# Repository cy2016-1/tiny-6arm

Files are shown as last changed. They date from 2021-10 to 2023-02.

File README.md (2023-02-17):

### 一、机械臂简介

机械制作方面采用铝型材、3D打印、同步带和步进电机，低成本的制作方案。控制器方面，使用esp32s3芯片，带有WiFi蓝牙功能。可以输出100KHZ脉冲，支持关节运动和直线运动指令，150mA 8路输出，6~36V 8路输入，带光耦隔离。编程方面，采用blockly可视化编程，使用手机或平板就可以完成编程。

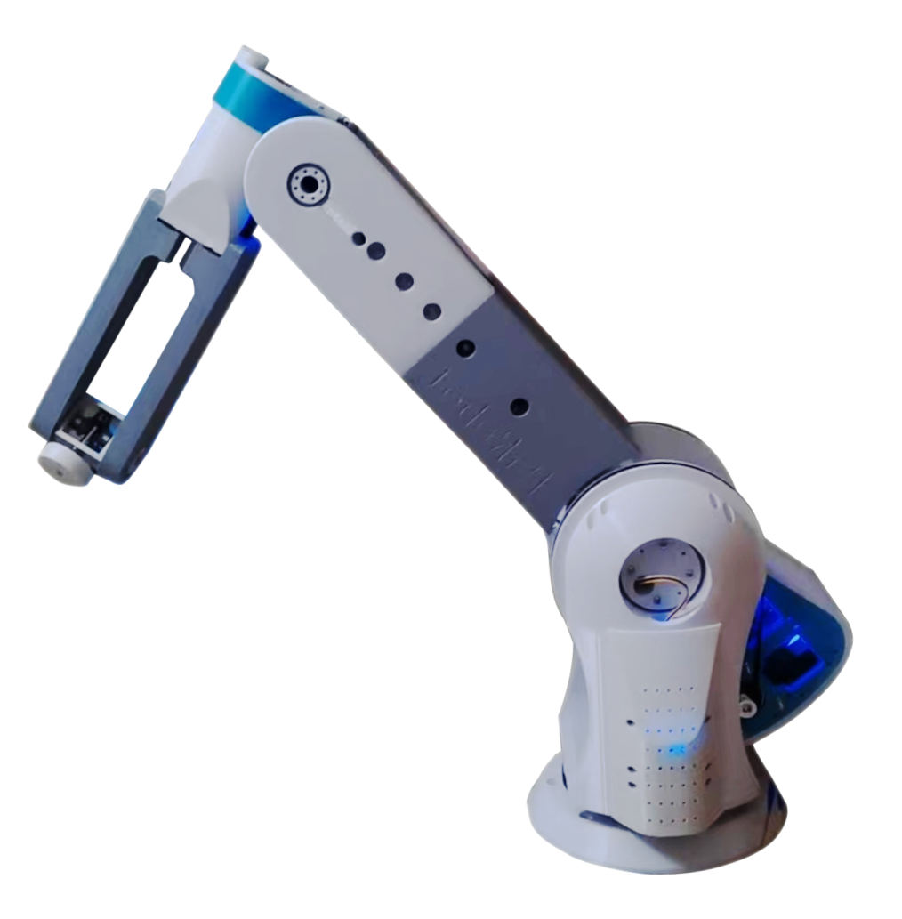
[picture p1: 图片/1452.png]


### 二、制作过程

#### 1.机械部分

首先使用FreeCAD软件进行3D模型图绘制。FreeCAD是一个开源的3D设计软件，可以免费使用，方便二次开发，支持运动仿真和简单的有限元仿真。我使用它来设计我的机械臂。其中前三关节采用双电机结构，也就是说一个关节有两个电机，这样平衡的设计既提高了负载能力，也提高了精度和稳定性。现在这台机械臂拥有3kg负载能力和0.5mm的重複定位精度，以及765mm的臂长。

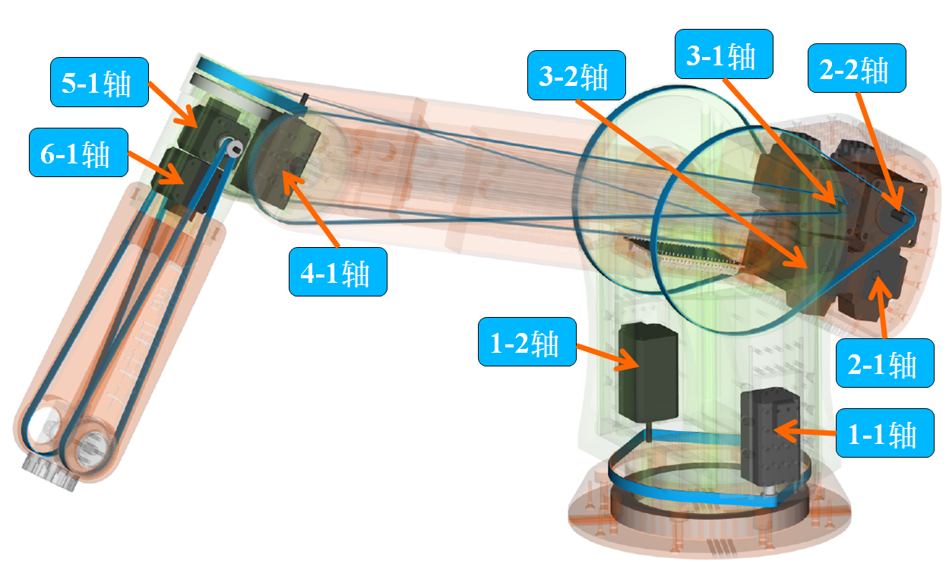
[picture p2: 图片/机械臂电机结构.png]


#### 2.控制器部分

##### 2.1 主控制器

主控制器采用ESP32-S3芯片，ESP32-S3芯片带有WiFi蓝牙功能，双核，240Mhz频率，45 个可编程 GPIO。性能可以满足机械臂运行算法，设计了6个脉冲控制接口，可以控制6轴机械臂。8路输入和8路输出，带光电耦合起到保护电路的作用，方便外接电磁阀。

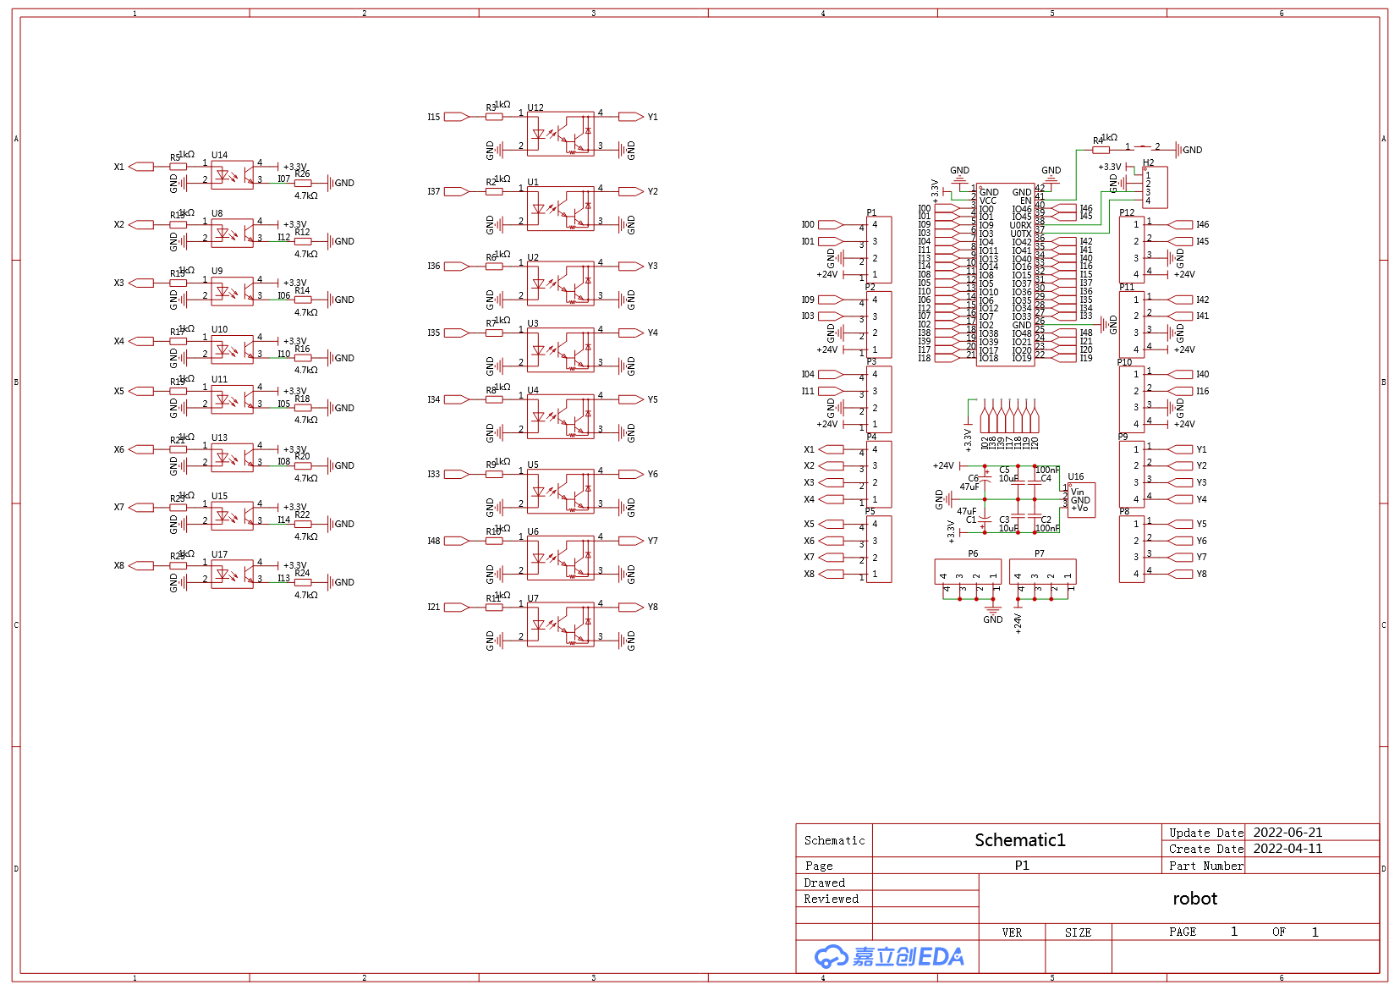
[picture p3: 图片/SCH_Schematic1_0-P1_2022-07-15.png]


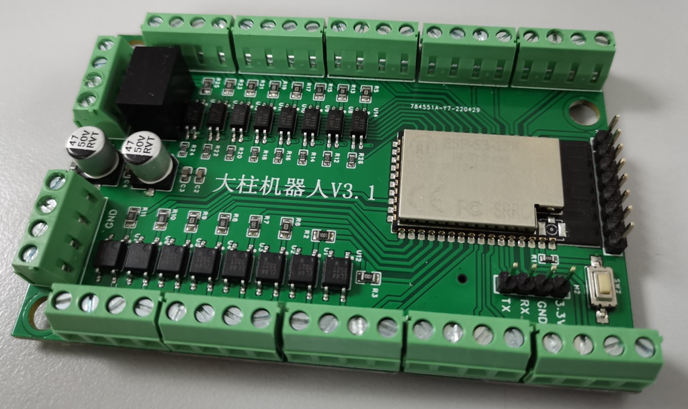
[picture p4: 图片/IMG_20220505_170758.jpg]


##### 2.2 电机驱动部分

步进电机驱动采用TB67S109AFTG芯片，支持最大4A电流。控制芯片使用ESP32-C3，支持脉冲控制和CAN通信控制。磁编码器使用MT6816CT-ACD，14位单圈绝度编码器，最高精度可达0.02°。

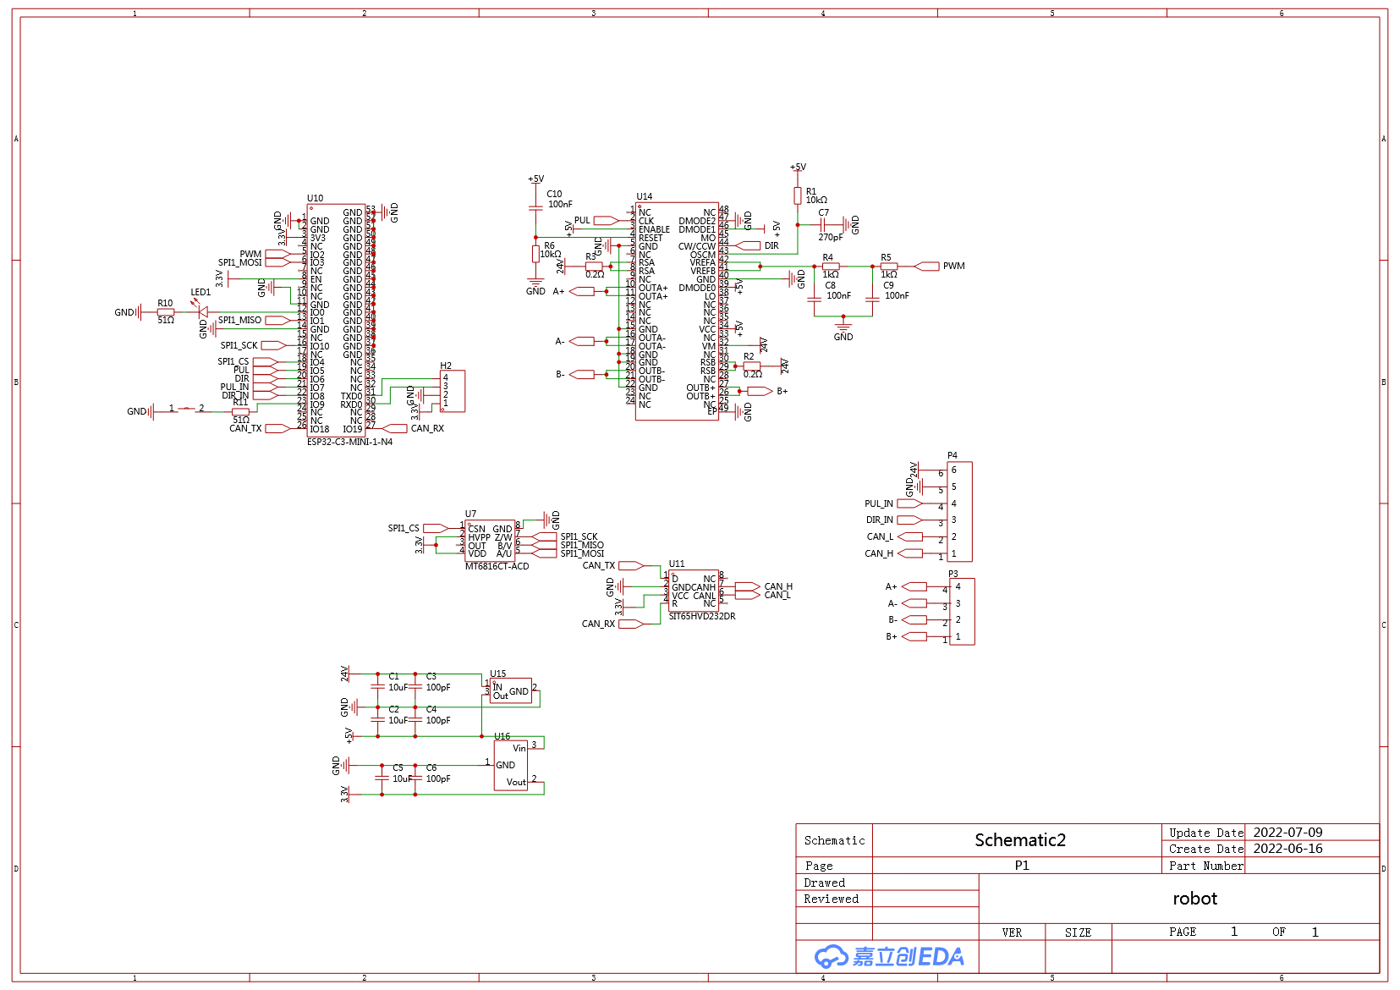
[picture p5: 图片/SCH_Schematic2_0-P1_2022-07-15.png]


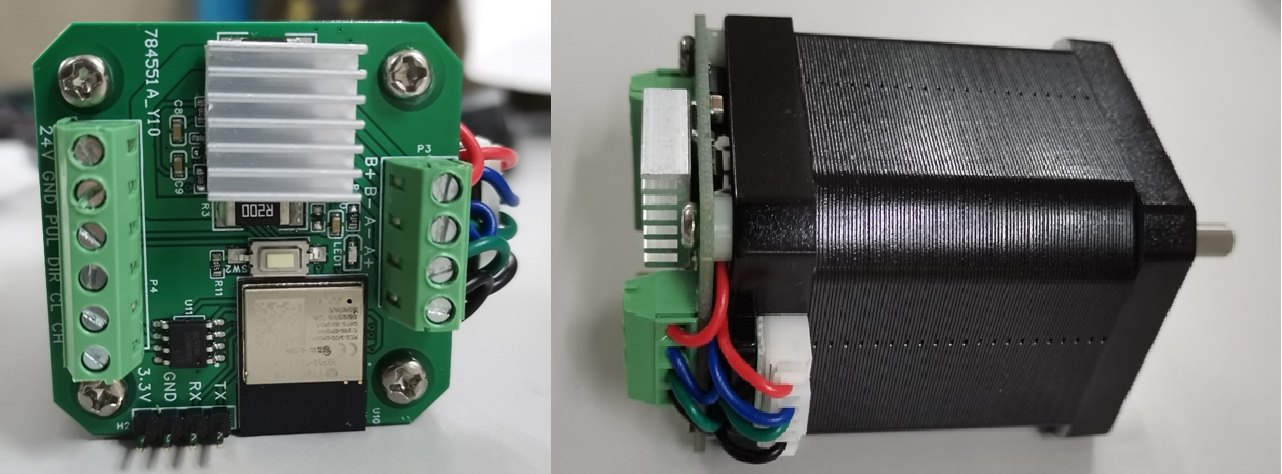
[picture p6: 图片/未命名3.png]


##### 2.3 软件部分

主控板程序是基于开源micropython的，它实现了使用python语言就可完成单片机程序开发。驱动板编程是基于ESP-IDF库编写的C语言程序。手机控制软件是基于开源blockly和bipes编写的。

软件下载时使用USB转串口下载，电机驱动板下载前按住按键然后上电进入下载模式，下载完成后需要校准编码器。校准方法是：电机无负载上电 >> 蓝色LED亮时按住按键 >> 进入自动校准模式。

| 电路板 | 程序 | 固件 |
|---|---|---|
| 控制器 | robot.c | robot.bin |
| 1-1轴 | step1-1.c  | step1-1.bin |
| 1-2轴 | step1-2.c  | step1-2.bin |
| 2-1轴 | step2-1.c  | step2-1.bin |
| 2-2轴 | step2-1.c  | step2-2.bin |
| 3-1轴 | step3-1.c  | step3-1.bin |
| 3-2轴 | step3-2.c  | step3-2.bin |
| 4-1轴 | step4-1.c  | step4-1.bin |
| 5-1轴 | step5-1.c  | step5-1.bin |
| 6-1轴 | step6-1.c  | step6-1.bin |

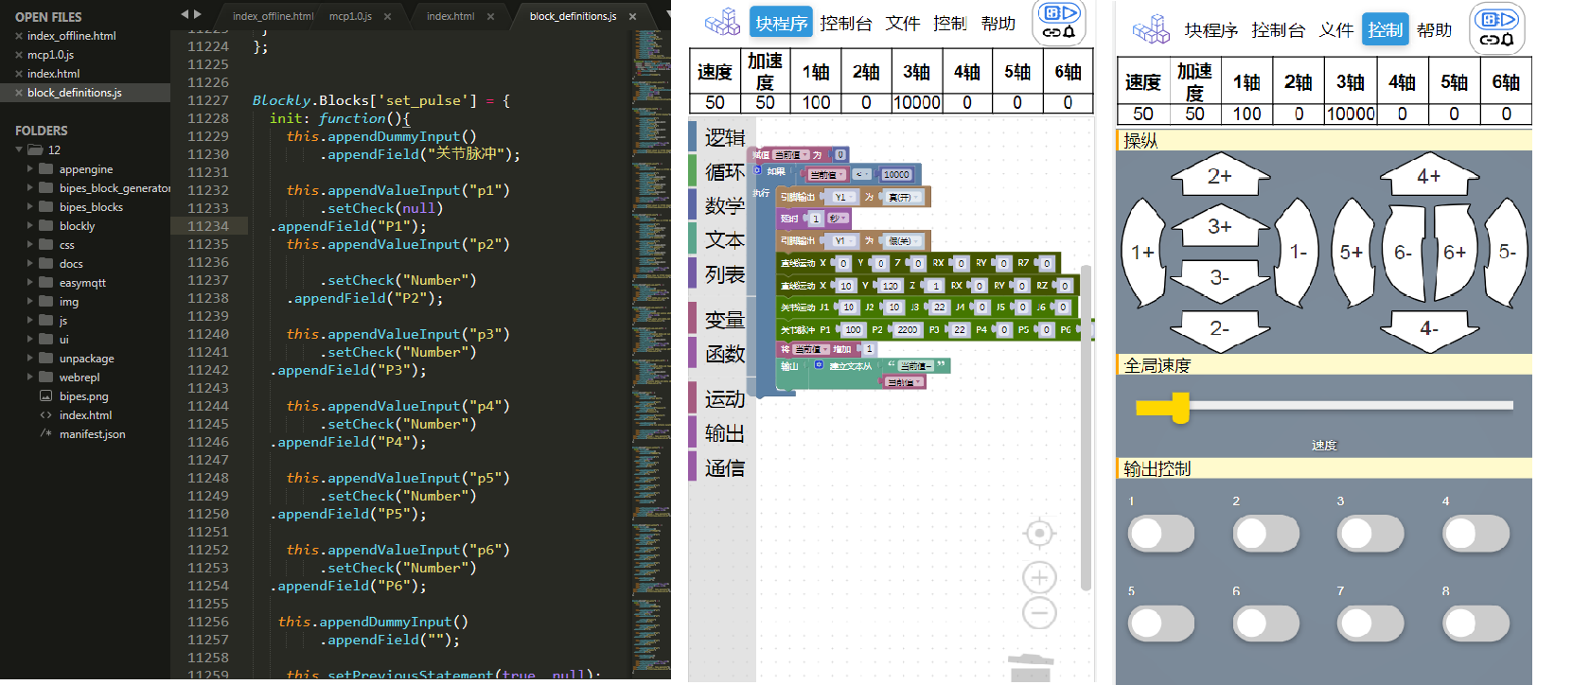
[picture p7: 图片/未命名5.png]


### 三、使用说明

注意：用手拖动到初始位置再通电，此时作为坐标原点。

#### 3.1 手机或平板编程

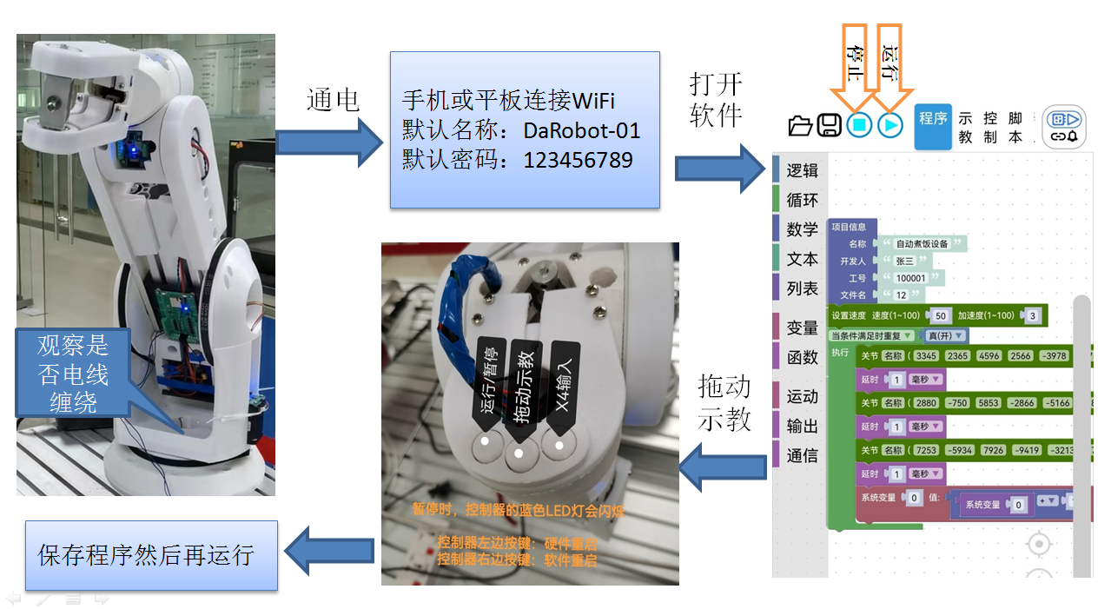
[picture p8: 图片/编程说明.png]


#### 3.2 电脑编程（Thonny软件）

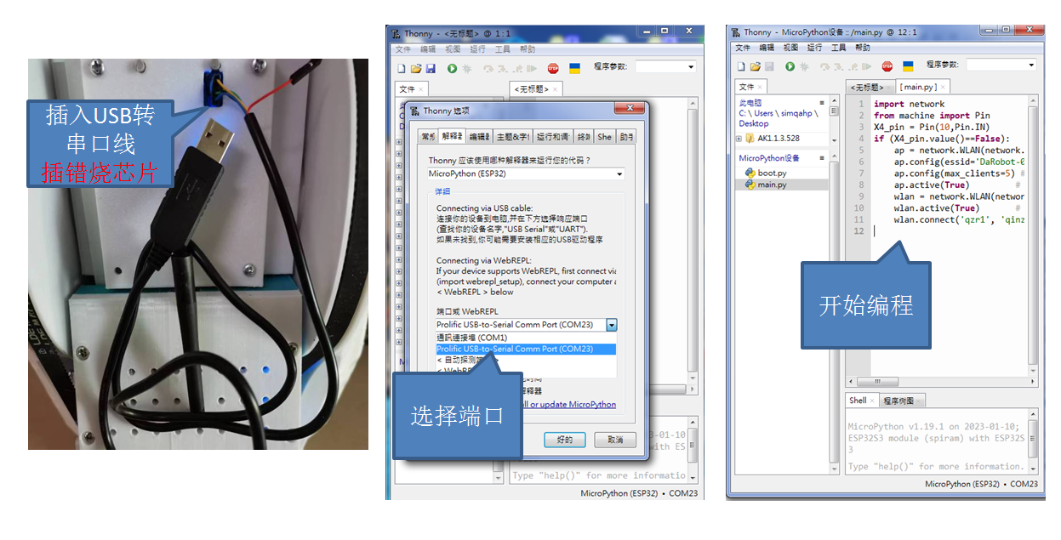
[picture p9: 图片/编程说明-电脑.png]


#### 3.3 RS485通信

控制板带有RS485通信接口，可以使用modbus协议控制和读取机械臂的状态

默认参数：波特率：9600，数据位：8，校验：无，停止位：1，modbus站口：1

| 地址 | 读/写 | 说明 |
|---|---|---|
| 0~99 | 读/写 | 系统变量，支持断电保存 |
| 100~149 | 读/写 | 未使用  |
| 150 | 读/写 | 机械臂全局速度 |
| 151 | 读 | 机械臂实时速度 |
| 152 | 读/写 | 机械臂目标速度 |
| 153 | 读 | 机械臂实时加速度 |
| 152 | 读/写 | 机械臂目标加速度 |
| 160~165 | 读 | 机械臂6个关节实时脉冲数  |
| 170~175 | 读/写 | 机械臂6个关节目标脉冲数  |
| 180~185 | 读 | 机械臂6个关节实时力矩  |
| 190 | 读/写 | 设置modbus波特率： 0:9600, 1:19200, 2:38400, 3:57600, 4:112500 |
| 191 | 读/写 | 设置modbus数据位： 0:8位,  1:7位 |
| 192 | 读/写 | 设置modbus校验： 0:无校验, 1:奇校验, 2:偶校验|
| 193 | 读/写 | 设置modbus停止位： 0:1位,  1:2位 |
| 194 | 读/写 | 设置modbus站口，默认是1，  范围：1~256 |

### 四、项目收入

| 时间 | 收入类型 | 金额（元） |
|---|---|---|
| 2021-2022 | 嘉立创-星火计划金奖 | 10000|
| 2021-2022 | 用户咨询赞助 | 500 |
| 2021-2022 | 哔哩哔哩视频 |  100 |
| 2020-2021 | 贸泽电子-短视频大赛金奖 | 2000  |
| 2020-2021 | 用户咨询赞助 | 200 |
| 2020-2021 | 哔哩哔哩视频 | 200 |

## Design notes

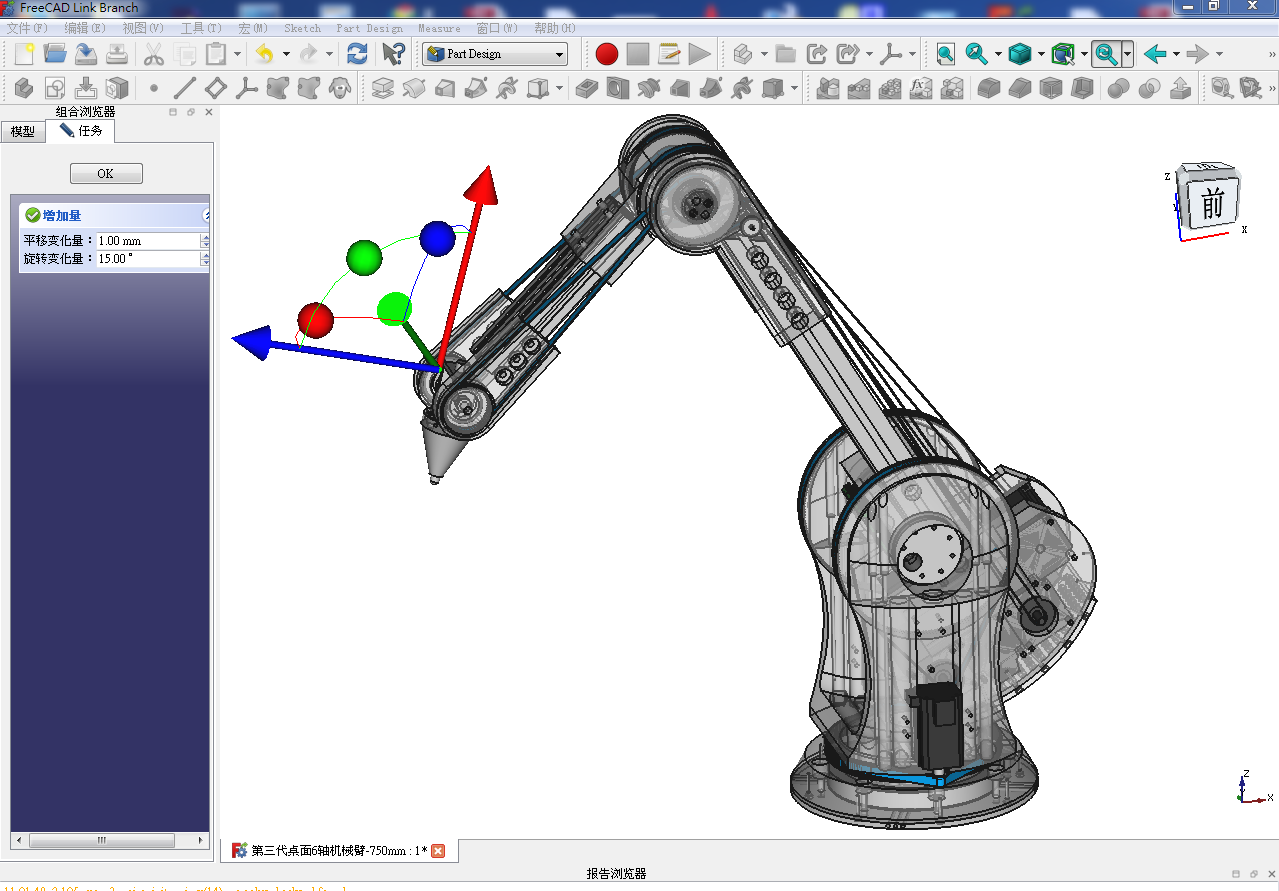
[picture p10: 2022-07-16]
图片未命名.png

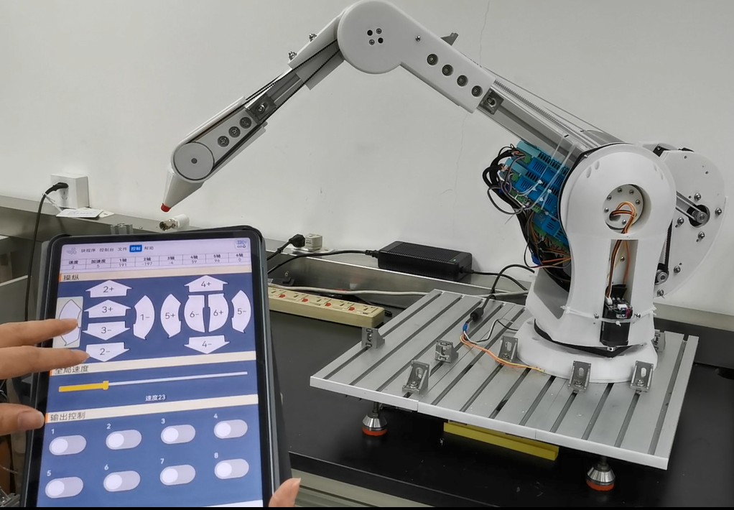
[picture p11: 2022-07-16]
图片/未命名4.png

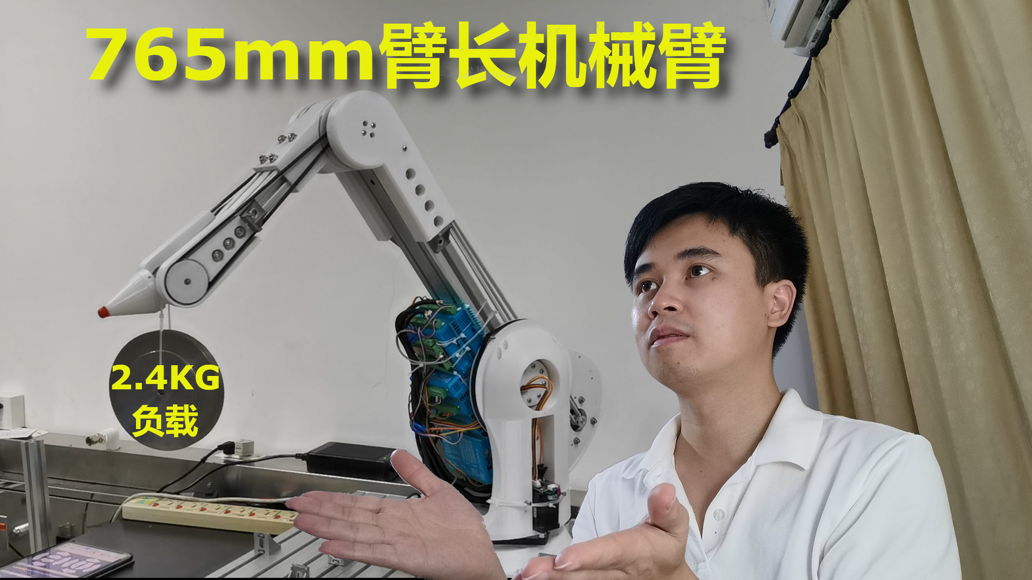
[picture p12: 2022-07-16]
图片/无标题8.png

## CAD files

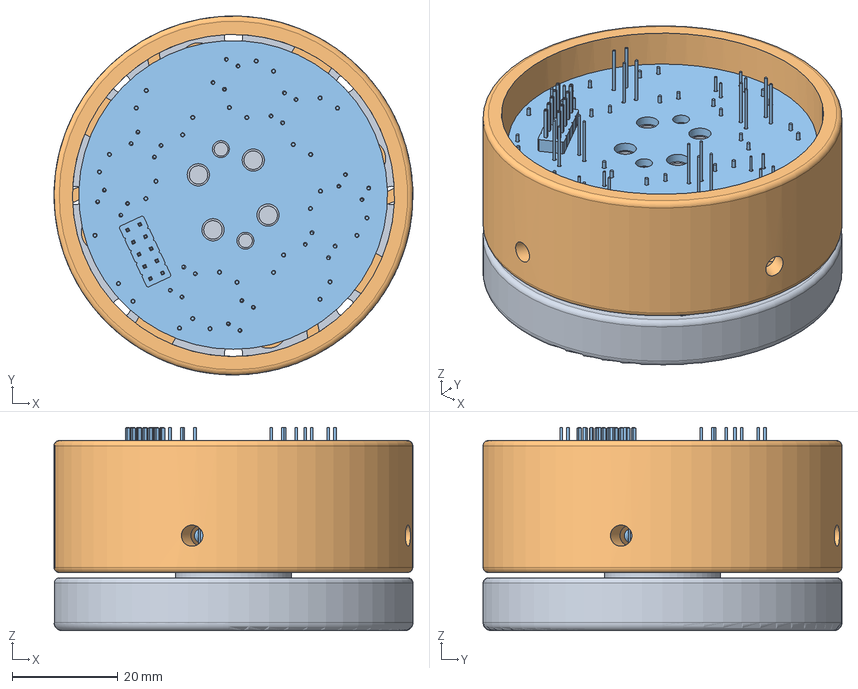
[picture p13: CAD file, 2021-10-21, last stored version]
3D模型图/力传感器.FCStd
68.0 x 68.0 x 38.5 mm
力传感器

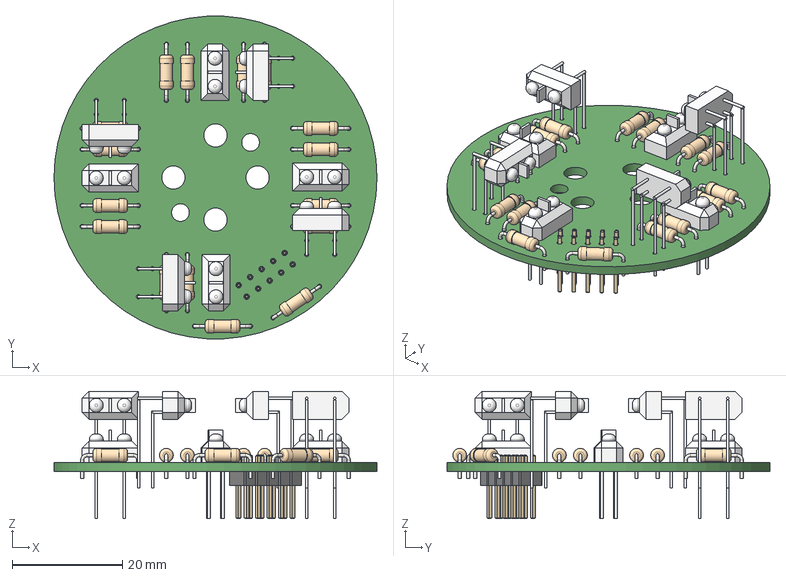
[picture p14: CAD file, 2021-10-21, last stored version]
力传感器电路图/力传感器.step
58.5 x 58.4 x 23.1 mm

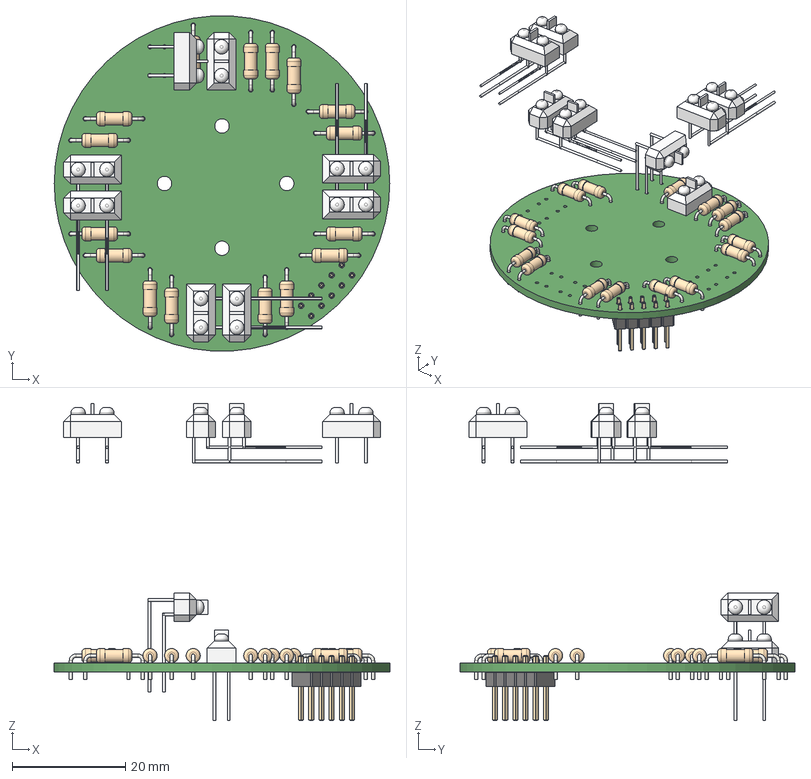
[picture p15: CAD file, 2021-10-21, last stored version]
力传感器电路图/力传感器22.step
59.2 x 59.1 x 56.0 mm

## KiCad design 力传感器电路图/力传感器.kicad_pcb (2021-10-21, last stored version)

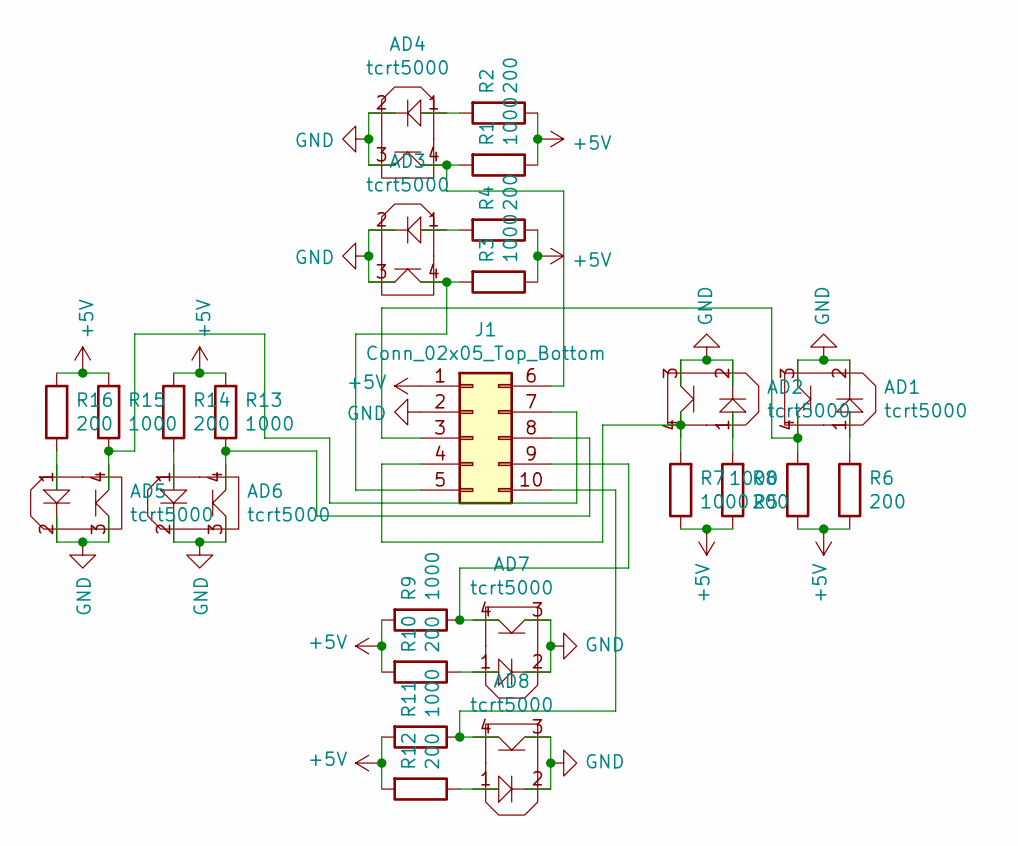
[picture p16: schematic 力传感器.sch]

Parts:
AD1, AD2, AD3, AD4, AD5, AD6, AD7, AD8: tcrt5000
J1: Conn_02x05_Top_Bottom; PinHeader_2x05_P2.54mm_Vertical
R1, R3, R5, R7, R9, R11, R13, R15: 1000; R_Axial_DIN0207_L6.3mm_D2.5mm_P10.16mm_Horizontal
R2, R4, R6, R8, R10, R12, R14, R16: 200; R_Axial_DIN0207_L6.3mm_D2.5mm_P10.16mm_Horizontal

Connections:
+5V: J1.1, R1.1, R2.1, R3.1, R4.1, R5.2, R6.1, R7.1, R8.1, R9.2, R10.2, R11.2, R12.2, R13.2, R14.2, R15.2, R16.2
GND: AD1.2, AD1.3, AD2.2, AD2.3, AD3.2, AD3.3, AD4.2, AD4.3, AD5.2, AD5.3, AD6.2, AD6.3, AD7.2, AD7.3, AD8.2, AD8.3, J1.2
unnamed: AD1.1, R6.2
unnamed: AD1.4, J1.3, R5.1
unnamed: AD2.1, R8.2
unnamed: AD2.4, J1.4, R7.2
unnamed: AD3.1, R4.2
unnamed: AD3.4, J1.5, R3.2
unnamed: AD4.1, R2.2
unnamed: AD4.4, J1.6, R1.2
unnamed: AD5.1, R16.1
unnamed: AD5.4, J1.7, R15.1
unnamed: AD6.1, R14.1
unnamed: AD6.4, J1.8, R13.1
unnamed: AD7.1, R10.1
unnamed: AD7.4, J1.9, R9.1
unnamed: AD8.1, R12.1
unnamed: AD8.4, J1.10, R11.1

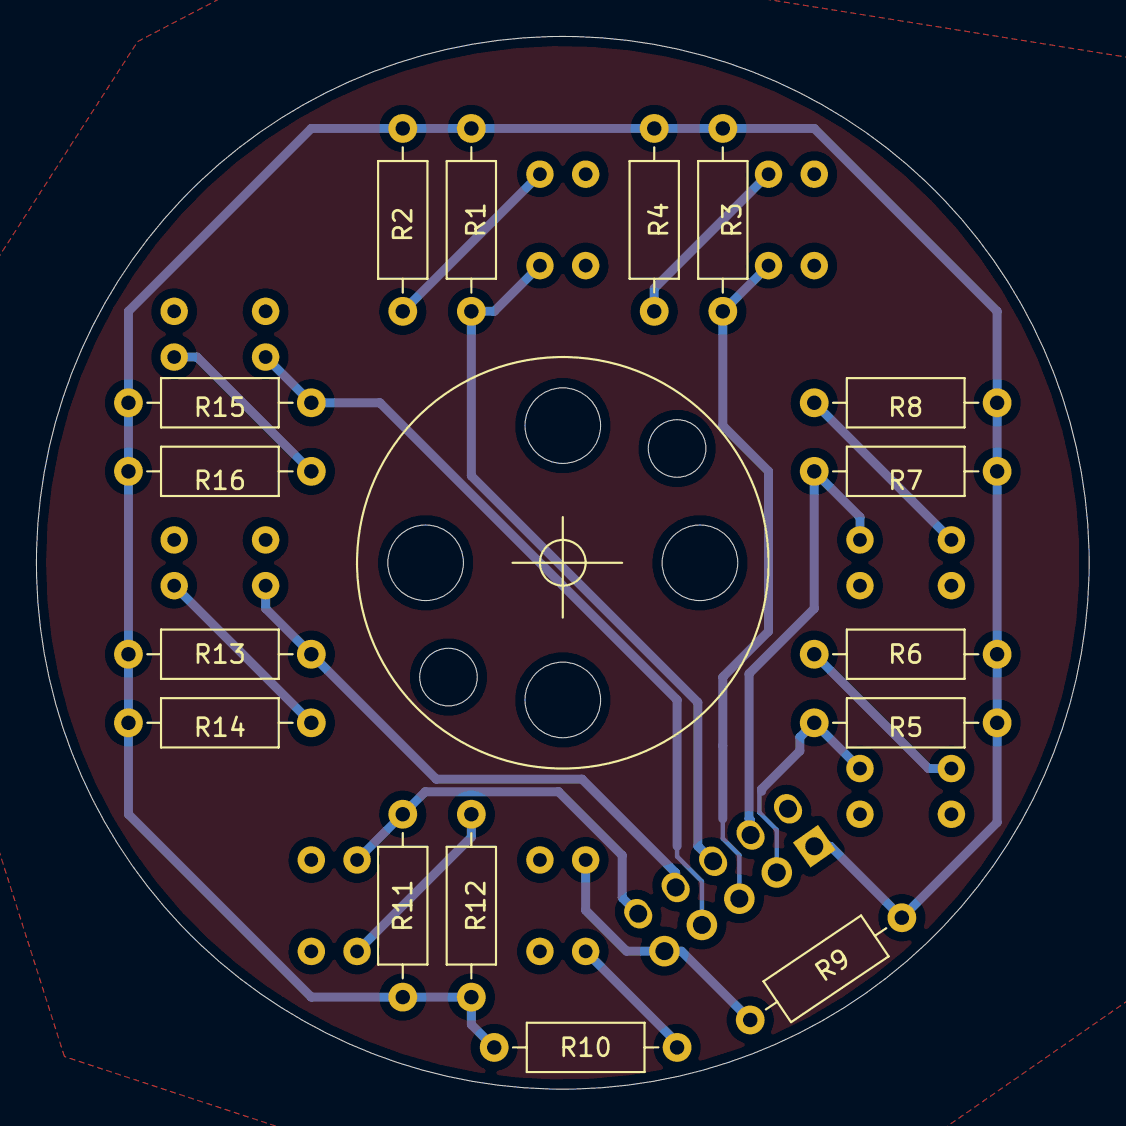
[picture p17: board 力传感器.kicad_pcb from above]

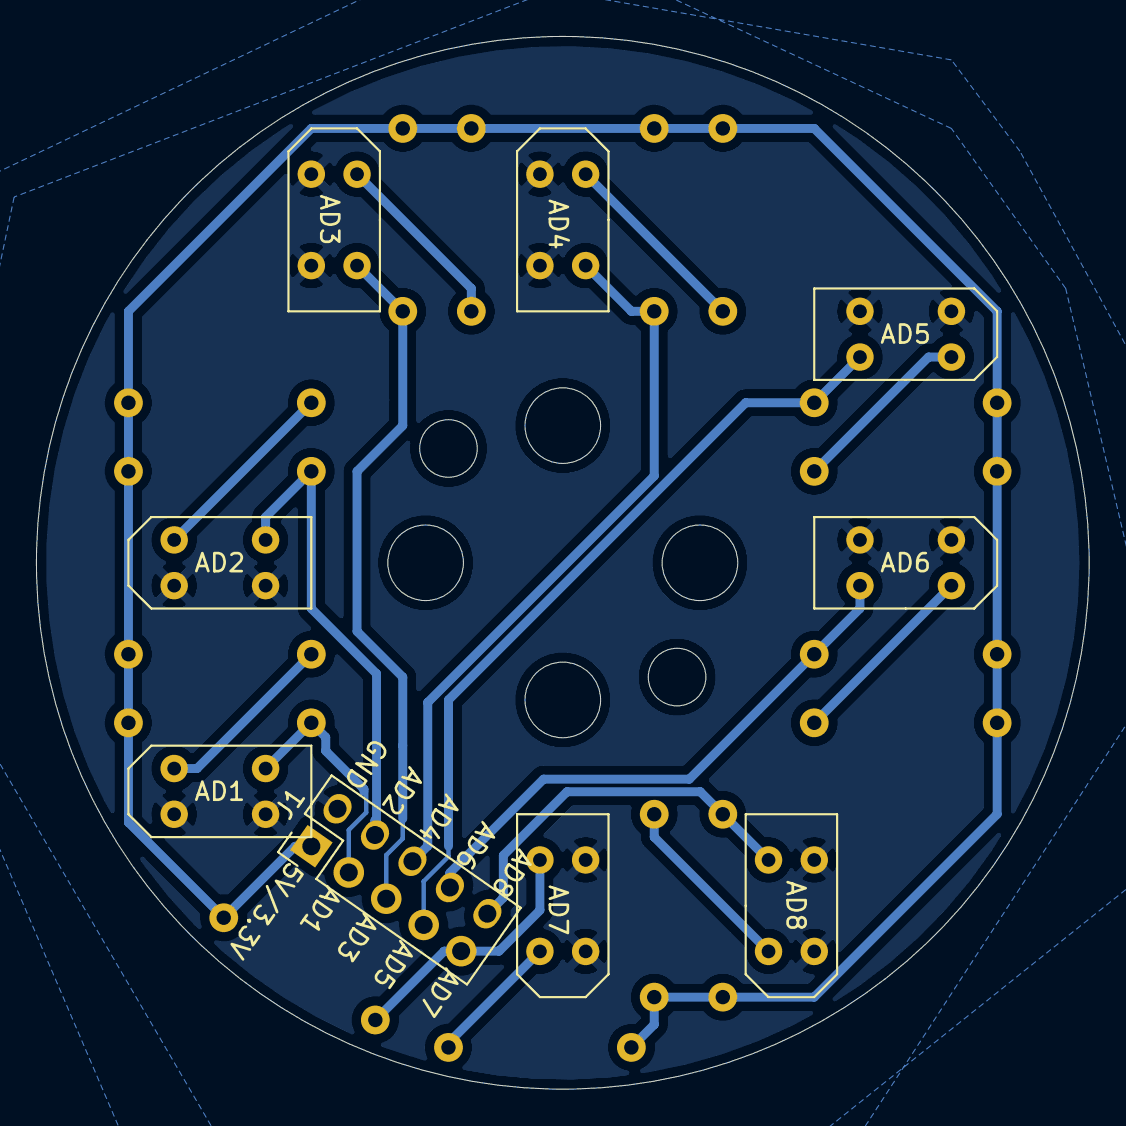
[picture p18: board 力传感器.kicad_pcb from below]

Board: 2 copper layers, 58.5 x 58.5 mm, 25 parts (9 on the bottom side), 18 nets.

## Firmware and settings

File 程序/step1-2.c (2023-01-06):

#include "freertos/FreeRTOS.h"
#include "esp_wifi.h"
#include "esp_system.h"
#include "esp_event.h"
#include "esp_event_loop.h"
#include "nvs_flash.h"
#include "driver/gpio.h"
#include "driver/spi_master.h"
#include "esp_log.h"
#include "driver/ledc.h"
#include "driver/timer.h"
#include "esp32/rom/ets_sys.h"
#include "math.h"
#include <stdio.h>
#include <stdlib.h>
#include <string.h>
#include "driver/twai.h"
#define DMA_CHAN        2
#define PIN_NUM_MISO    10
#define PIN_NUM_MOSI    3
#define PIN_NUM_CLK     1
#define PIN_NUM_CS      4

#define STORAGE_NAMESPACE "storage"

#define TIMER_DIVIDER         (2)  //  Hardware timer clock divider
#define TIMER_SCALE           ((6*10)/(TIMER_DIVIDER))  // convert counter value to seconds



#define LEDC_TIMER              LEDC_TIMER_0
#define LEDC_MODE               LEDC_LOW_SPEED_MODE
#define LEDC_OUTPUT_IO          (2) // Define the output GPIO
#define LEDC_CHANNEL            LEDC_CHANNEL_0
#define LEDC_DUTY_RES           LEDC_TIMER_10_BIT // Set duty resolution to 13 bits
#define LEDC_DUTY               (100) // Set duty to 50%. ((2 ** 13) - 1) * 50% = 4095
#define LEDC_FREQUENCY          (20000) // Frequency in Hertz. Set frequency at 5 kHz

#define STEP_EN  5
#define STEP_PUL 6
#define STEP_DIR 7

#define LED_OI   0
#define KEY_OI   9

#define CAN_TX   18
#define CAN_RX   19

static const char TAG[] = "main";


typedef struct {
    int timer_group;
    int timer_idx;
    int alarm_interval;
    bool auto_reload;
} example_timer_info_t;

typedef struct {
    example_timer_info_t info;
    uint64_t timer_counter_value;
} example_timer_event_t;


esp_err_t event_handler(void *ctx, system_event_t *event)
{
    return ESP_OK;
}





static void pwm_init(void)
{
    // Prepare and then apply the LEDC PWM timer configuration
    ledc_timer_config_t ledc_timer = {
        .speed_mode       = LEDC_MODE,
        .timer_num        = LEDC_TIMER,
        .duty_resolution  = LEDC_DUTY_RES,
        .freq_hz          = LEDC_FREQUENCY,  // Set output frequency at 5 kHz
        .clk_cfg          = LEDC_AUTO_CLK
    };
    ESP_ERROR_CHECK(ledc_timer_config(&ledc_timer));

    // Prepare and then apply the LEDC PWM channel configuration
    ledc_channel_config_t ledc_channel = {
        .speed_mode     = LEDC_MODE,
        .channel        = LEDC_CHANNEL,
        .timer_sel      = LEDC_TIMER,
        .intr_type      = LEDC_INTR_DISABLE,
        .gpio_num       = LEDC_OUTPUT_IO,
        .duty           = 0, // Set duty to 0%
        .hpoint         = 0
    };
    ESP_ERROR_CHECK(ledc_channel_config(&ledc_channel));
}
int first_angle = 0;
long step_pul = 0;
long tar_pul = 0;
long step_angle = 0;
long pwm = 0;
long max_pwm = 0;
int num=0;
int key = 20;
int circle = 0;
int step_circle = 0;
int pre_angle = 0;
int cur_angle = 0;
int8_t up_foc = 100;
int8_t down_foc = 100;
uint8_t min_pwm = 0;
uint16_t Encoder_calibration[3200];
int is_calibration = 0;
int calibration_num = 0;
int is_save_calibration = 0;

spi_transaction_t t = {
	.length = 16,
	.addr = 0x83,
	.flags = SPI_TRANS_USE_RXDATA,
	.user = (void*)1,
};
esp_err_t ret;
spi_device_handle_t spi;


static const twai_timing_config_t t_config = TWAI_TIMING_CONFIG_500KBITS();
static const twai_filter_config_t f_config = TWAI_FILTER_CONFIG_ACCEPT_ALL();
static const twai_general_config_t g_config = TWAI_GENERAL_CONFIG_DEFAULT(CAN_TX, CAN_RX, TWAI_MODE_NO_ACK);



static bool IRAM_ATTR timer_group_isr_callback(void *args)
{
    BaseType_t high_task_awoken = pdFALSE;
    gpio_set_level(STEP_PUL, 0);

    num ++;
    if((num%2)==0)
    {
    	pre_angle = cur_angle;

        gpio_set_level(PIN_NUM_CS, 0);
    	ret = spi_device_polling_transmit(spi, &t);
    	gpio_set_level(PIN_NUM_CS, 1);

    	cur_angle = (t.rx_data[0]*64+t.rx_data[1]/4);
    	if(cur_angle<1000&&pre_angle>15000)circle++;
    	if(cur_angle>15000&&pre_angle<1000)circle--;
    	step_angle = circle*16384+cur_angle;
    	pwm = labs(step_angle-(step_circle*16384+Encoder_calibration[(step_pul%3200)<0?(step_pul%3200+3200):(step_pul%3200)]));
    	pwm = (pwm*pwm*6);
    	if(pwm>60000)pwm = 60000;
    	if(pwm<2)pwm = 2;
    	if(max_pwm<pwm)max_pwm = pwm;
    	else max_pwm = max_pwm - 2;
    	if(max_pwm<2)max_pwm = 2;
        if(is_calibration==1)ledc_set_duty(LEDC_MODE, LEDC_CHANNEL, 300);
    	else ledc_set_duty(LEDC_MODE, LEDC_CHANNEL, (max_pwm/100)+min_pwm*10);
    	ledc_update_duty(LEDC_MODE, LEDC_CHANNEL);
    }


    if(is_calibration==1)
    {
    	if((num%1000)==0)
    	{
    		Encoder_calibration[(step_pul+calibration_num)%3200]=cur_angle;
			gpio_set_level(STEP_DIR, 1);
			gpio_set_level(STEP_PUL, 1);
    		calibration_num++;
    		if(calibration_num>=3200)
			{
    			is_calibration = 0;
    			calibration_num = 0;
    			is_save_calibration = 1;
			}
    	}
    }
    else if(is_calibration==0)
	{
		if((step_angle-(step_circle*16384+Encoder_calibration[(step_pul%3200)<0?(step_pul%3200+3200):(step_pul%3200)]))>up_foc)
		{
			gpio_set_level(STEP_DIR, 1);
			gpio_set_level(STEP_PUL, 1);
			step_pul+=1;
			if(Encoder_calibration[((step_pul-1)%3200)<0?((step_pul-1)%3200+3200):((step_pul-1)%3200)]-Encoder_calibration[((step_pul)%3200)<0?((step_pul)%3200+3200):((step_pul)%3200)]>1000)step_circle++;
		}

		else if((step_angle-(step_circle*16384+Encoder_calibration[(step_pul%3200)<0?(step_pul%3200+3200):(step_pul%3200)]))<-down_foc)
		{
			gpio_set_level(STEP_DIR, 0);
			gpio_set_level(STEP_PUL, 1);
			step_pul-=1;
			if(Encoder_calibration[((step_pul+1)%3200)<0?((step_pul+1)%3200+3200):((step_pul+1)%3200)]-Encoder_calibration[((step_pul)%3200)<0?((step_pul)%3200+3200):((step_pul)%3200)]<-1000)step_circle--;
		}

		else if((tar_pul-step_pul)>1&&(num%(1000/((tar_pul-step_pul))+1)==0))
		{
			gpio_set_level(STEP_DIR, 1);
			gpio_set_level(STEP_PUL, 1);
			step_pul+=1;
			if(Encoder_calibration[((step_pul-1)%3200)<0?((step_pul-1)%3200+3200):((step_pul-1)%3200)]-Encoder_calibration[((step_pul)%3200)<0?((step_pul)%3200+3200):((step_pul)%3200)]>1000)step_circle++;

		}
		else if((tar_pul-step_pul)<-1&&(num%(1000/((-tar_pul+step_pul))+1)==0))
		{
			gpio_set_level(STEP_DIR, 0);
			gpio_set_level(STEP_PUL, 1);
			step_pul-=1;
			if(Encoder_calibration[((step_pul+1)%3200)<0?((step_pul+1)%3200+3200):((step_pul+1)%3200)]-Encoder_calibration[((step_pul)%3200)<0?((step_pul)%3200+3200):((step_pul)%3200)]<-1000)step_circle--;

		}


	}

    return high_task_awoken == pdTRUE; // return whether we need to yield at the end of ISR

}

static void example_tg_timer_init(int group, int timer, bool auto_reload, int timer_interval_sec)
{
    /* Select and initialize basic parameters of the timer */
    timer_config_t config = {
        .divider = TIMER_DIVIDER,
        .counter_dir = TIMER_COUNT_UP,
        .counter_en = TIMER_PAUSE,
        .alarm_en = TIMER_ALARM_EN,
        .auto_reload = auto_reload,
    }; // default clock source is APB
    timer_init(group, timer, &config);

    /* Timer's counter will initially start from value below.
       Also, if auto_reload is set, this value will be automatically reload on alarm */
    timer_set_counter_value(group, timer, 0);

    /* Configure the alarm value and the interrupt on alarm. */
    timer_set_alarm_value(group, timer, timer_interval_sec * TIMER_SCALE);
    timer_enable_intr(group, timer);

    example_timer_info_t *timer_info = calloc(1, sizeof(example_timer_info_t));
    timer_info->timer_group = group;
    timer_info->timer_idx = timer;
    timer_info->auto_reload = auto_reload;
    timer_info->alarm_interval = timer_interval_sec;
    timer_isr_callback_add(group, timer, timer_group_isr_callback, timer_info, 0);

    timer_start(group, timer);
}

int32_t err_step = 0;
int8_t is_fist_rec = 1;
static void twai_receive_task(void *arg)
{
    while (1) {
        twai_message_t rx_msg;
        twai_receive(&rx_msg, portMAX_DELAY);
        if (rx_msg.identifier == 0x0B1) 
        {   
            int32_t data = 0;
            for (int i = 0; i < 4; i++) {
                data |= (rx_msg.data[i] << (i * 8));
            }
            if(is_fist_rec)
            {
                err_step = -data+tar_pul;
                is_fist_rec = 0;
            }
            tar_pul = err_step + data;
            gpio_set_level(LED_OI, 1);
        }
        else if (rx_msg.identifier == 0x0C1)
        {
            up_foc = rx_msg.data[0];
            down_foc = rx_msg.data[1];
            min_pwm = rx_msg.data[2];
            if(rx_msg.data[3]==1)tar_pul = step_pul;
            gpio_set_level(LED_OI, 1);
        }
    }
    vTaskDelete(NULL);
}



static void run_task(void *arg)
{
    vTaskDelay(3000 / portTICK_PERIOD_MS);
    while (1) {
        // twai_message_t tx_msg = {.data_length_code = 8, .identifier = 0x0A1};
        // tx_msg.data[0] =  step_pul & 0x000000ff; 
        // tx_msg.data[1] = (step_pul & 0x0000ff00) >> 8; 
        // tx_msg.data[2] = (step_pul & 0x00ff0000) >> 16;
        // tx_msg.data[3] = (step_pul & 0xff000000) >> 24;
        // tx_msg.data[4] = up_foc;
        // tx_msg.data[5] = down_foc;
        // tx_msg.data[6] = max_pwm/1000;  
        // tx_msg.data[7] = min_pwm;                
        // twai_transmit(&tx_msg, portMAX_DELAY);
        vTaskDelay(100 / portTICK_PERIOD_MS);
    }
    vTaskDelete(NULL);
}

void app_main(void)
{

    esp_err_t err = nvs_flash_init();
    if (err == ESP_ERR_NVS_NO_FREE_PAGES || err == ESP_ERR_NVS_NEW_VERSION_FOUND) {
        // NVS partition was truncated and needs to be erased
        // Retry nvs_flash_init
        ESP_ERROR_CHECK(nvs_flash_erase());
        err = nvs_flash_init();
    }
    ESP_ERROR_CHECK( err );
//    tcpip_adapter_init();
//    ESP_ERROR_CHECK( esp_event_loop_init(event_handler, NULL) );
//    wifi_init_config_t cfg = WIFI_INIT_CONFIG_DEFAULT();
//    ESP_ERROR_CHECK( esp_wifi_init(&cfg) );
//    ESP_ERROR_CHECK( esp_wifi_set_storage(WIFI_STORAGE_RAM) );
//    ESP_ERROR_CHECK( esp_wifi_set_mode(WIFI_MODE_STA) );
//    wifi_config_t sta_config = {
//        .sta = {
//            .ssid = CONFIG_ESP_WIFI_SSID,
//            .password = CONFIG_ESP_WIFI_PASSWORD,
//            .bssid_set = false
//        }
//    };
//    ESP_ERROR_CHECK( esp_wifi_set_config(WIFI_IF_STA, &sta_config) );
//    ESP_ERROR_CHECK( esp_wifi_start() );
//    ESP_ERROR_CHECK( esp_wifi_connect() );
    nvs_handle_t my_handle;
    size_t required_size = 6400;  // value will default to 0, if not set yet in NVS
    err = nvs_open(STORAGE_NAMESPACE, NVS_READWRITE, &my_handle);
    if (err != ESP_OK) ESP_LOGI(TAG, "Initializing nvs err");

    err = nvs_get_blob(my_handle, "Encoder", NULL, &required_size);
    if (err != ESP_OK && err != ESP_ERR_NVS_NOT_FOUND) ESP_LOGI(TAG, "get nvs num err");
    ESP_LOGI(TAG, "nvs num :%d",required_size);

    err = nvs_get_blob(my_handle, "Encoder", Encoder_calibration, &required_size);
    if (err != ESP_OK) ESP_LOGI(TAG, "get nvs err");
//	for(int i=0;i<3200;i++)
//	{
//		ESP_LOGI(TAG, "Encoder_calibration[%d]=%d",i,Encoder_calibration[i]);
//	}

    // Set the LEDC peripheral configuration
    pwm_init();
    // Set duty to 50%
    ESP_ERROR_CHECK(ledc_set_duty(LEDC_MODE, LEDC_CHANNEL, 50));
    // Update duty to apply the new value
    ESP_ERROR_CHECK(ledc_update_duty(LEDC_MODE, LEDC_CHANNEL));




    ESP_LOGI(TAG, "Initializing bus SPI%d...", SPI2_HOST+1);

    spi_bus_config_t buscfg={
        .miso_io_num = PIN_NUM_MISO,                // MISO信号线
        .mosi_io_num = PIN_NUM_MOSI,                // MOSI信号线
        .sclk_io_num = PIN_NUM_CLK,                 // SCLK信号线
        .quadwp_io_num = -1,                        // WP信号线，专用于QSPI的D2
        .quadhd_io_num = -1,                        // HD信号线，专用于QSPI的D3
        .max_transfer_sz = 32,                    // 最大传输数据大小
    };

    spi_device_interface_config_t devcfg={
//    	.command_bits = 16,
		.address_bits = 8,
        .clock_speed_hz = SPI_MASTER_FREQ_10M,      // Clock out at 10 MHz,
//        .flags = SPI_DEVICE_HALFDUPLEX | SPI_DEVICE_POSITIVE_CS,
//        .pre_cb = cs_high,
//        .post_cb = cs_low,
		.input_delay_ns =200,
		.mode = 3,                                  // SPI mode 0
        /*
         * The timing requirements to read the busy signal from the EEPROM cannot be easily emulated
         * by SPI transactions. We need to control CS pin by SW to check the busy signal manually.
         */
        .spics_io_num = -1,
        .queue_size = 2,                            // 传输队列大小，决定了等待传输数据的数量
    };

    //Initialize the SPI bus
    ret = spi_bus_initialize(SPI2_HOST, &buscfg, 3);
    ESP_ERROR_CHECK(ret);

    ret = spi_bus_add_device(SPI2_HOST, &devcfg, &spi);
    ESP_ERROR_CHECK(ret);





//    gpio_pad_select_gpio(PIN_NUM_CS);                // 选择一个GPIO
    //zero-initialize the config structure.
    gpio_config_t io_conf = {};
    //disable interrupt
    io_conf.intr_type = GPIO_INTR_DISABLE;
    //set as output mode
    io_conf.mode = GPIO_MODE_OUTPUT;
    //bit mask of the pins that you want to set,e.g.GPIO18/19
    io_conf.pin_bit_mask =
    		((1ULL<<PIN_NUM_CS)|(1ULL<<STEP_EN)|(1ULL<<STEP_PUL)|(1ULL<<STEP_DIR)|
            (1ULL<<CAN_TX) |(1ULL<<LED_OI));
    //disable pull-down mode
    io_conf.pull_down_en = 1;
    //disable pull-up mode
    io_conf.pull_up_en = 1;
    //configure GPIO with the given settings
    gpio_config(&io_conf);


    gpio_config_t i_conf = {};
    //disable interrupt
    i_conf.intr_type = GPIO_INTR_DISABLE;
    //set as output mode
    i_conf.mode = GPIO_MODE_INPUT;
    //bit mask of the pins that you want to set,e.g.GPIO18/19
    i_conf.pin_bit_mask =
    		(1ULL<<CAN_RX);
    //disable pull-down mode
    i_conf.pull_down_en = 1;
    //disable pull-up mode
    i_conf.pull_up_en = 0;
    //configure GPIO with the given settings
    gpio_config(&i_conf);

    i_conf.pin_bit_mask =
    		((1ULL<<KEY_OI));
    //disable pull-down mode
    i_conf.pull_down_en = 0;
    //disable pull-up mode
    i_conf.pull_up_en = 1;
    //configure GPIO with the given settings
    gpio_config(&i_conf);


    gpio_set_level(CAN_TX, 1);

	ledc_set_duty(LEDC_MODE, LEDC_CHANNEL, 400);
    gpio_set_level(STEP_EN, 1);
	ledc_update_duty(LEDC_MODE, LEDC_CHANNEL);
	vTaskDelay(100 / portTICK_PERIOD_MS);

    gpio_set_level(PIN_NUM_CS, 1);
	vTaskDelay(10 / portTICK_PERIOD_MS);

    gpio_set_level(PIN_NUM_CS, 0);
	ret = spi_device_polling_transmit(spi, &t);
	gpio_set_level(PIN_NUM_CS, 1);
    gpio_set_level(PIN_NUM_CS, 0);
	ret = spi_device_polling_transmit(spi, &t);
	gpio_set_level(PIN_NUM_CS, 1);
	cur_angle = (t.rx_data[0]*64+t.rx_data[1]/4);
	pre_angle = cur_angle;

	// step_pul = (cur_angle/64)*64;
	// tar_pul = step_pul;
    gpio_set_level(LED_OI, 1);
    vTaskDelay(1000 / portTICK_PERIOD_MS);
    gpio_set_level(LED_OI, 0);
    if(gpio_get_level(KEY_OI)==0){
        // key--;
        // gpio_set_level(CAN_TX, key%2);
        is_calibration = 1;

    }else
    {
        ESP_LOGI(TAG, "cur_angle: %d", cur_angle);

        int min_angle = abs(cur_angle-Encoder_calibration[0]);
        ESP_LOGI(TAG, "min_angle: %d", min_angle);

        for(int i=0;i<3200;i+=64)
        {
            if(abs(cur_angle-Encoder_calibration[i]) < min_angle){
                min_angle = abs(cur_angle-Encoder_calibration[i]);
                ESP_LOGI(TAG, "min_angle: %d", min_angle);
                ESP_LOGI(TAG, "i: %d", i);
                step_pul = i;
                tar_pul = step_pul;
            } 

        }
        ESP_ERROR_CHECK(twai_driver_install(&g_config, &t_config, &f_config));
        ESP_ERROR_CHECK(twai_start());
        ESP_LOGI(TAG, "Driver started");
        xTaskCreatePinnedToCore(twai_receive_task, "TWAI_rx", 4096, NULL, 8, NULL, tskNO_AFFINITY);
        xTaskCreatePinnedToCore(run_task, "run_task", 4096, NULL, 7, NULL, tskNO_AFFINITY);

    }
   

    example_tg_timer_init(TIMER_GROUP_0, TIMER_0, true, 10);

    int level = 0;
    while (true) {
        // gpio_set_level(CAN_TX, 0);

    	if(is_save_calibration)
    	{
    	    err = nvs_set_blob(my_handle, "Encoder", Encoder_calibration, 6400);
    	    if (err != ESP_OK) ESP_LOGI(TAG, "set nvs err");
    	    // Commit
    	    err = nvs_commit(my_handle);
    	    if (err != ESP_OK) ESP_LOGI(TAG, "nvs commit err");

    	    // Close
    	    nvs_close(my_handle);
			for(int i=0;i<3200;i++)
			{
				ESP_LOGI(TAG, "Encoder_calibration[%d]=%d",i,Encoder_calibration[i]);
			}
			is_save_calibration = 0;
    	}
        gpio_set_level(LED_OI, 0);
        ESP_LOGI(TAG, "tar_pul: %ld", tar_pul);
        ESP_LOGI(TAG, "cur_angle: %d", cur_angle);
        ESP_LOGI(TAG, "step_angle: %ld", step_angle);
        ESP_LOGI(TAG, "step_pul: %ld", step_pul);
        ESP_LOGI(TAG, "step: %d", cur_angle/64);
        ESP_LOGI(TAG, "max_pwm: %ld", max_pwm);
        ESP_LOGI(TAG, "Encoder_calibration[%d]: %d",step_pul%3200<0?(step_pul%3200+3200):(step_pul%3200), (step_circle*16384+Encoder_calibration[((step_pul%3200)<0)?((step_pul%3200)+3200):(step_pul%3200)]));
        level = !level;            

        vTaskDelay(200 / portTICK_PERIOD_MS);


    }
}

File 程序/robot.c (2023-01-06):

#include "py/obj.h"
#include "py/runtime.h"
#include "py/mphal.h"
#include "driver/gpio.h"
#include "esp_event.h"
#include "driver/timer.h"
#include "math.h"
#include "freertos/task.h"
#include <esp_http_server.h>
#include "cJSON.h"
//#include "extmod/vfs.h"
#include "esp_log.h"
#include "esp_vfs.h"
#include "esp_vfs_fat.h"
#include "nvs_flash.h"
#include "esp_log.h"
#include "esp_spiffs.h"
#include "esp_littlefs.h"
#include "driver/twai.h"
#include "driver/uart.h"
#include "esp_log.h"
#define TIMER_DIVIDER         (2)  //  Hardware timer clock divider
#define TIMER_SCALE           ((8*10)/(TIMER_DIVIDER))  // convert counter value to seconds


// #define TX_485      GPIO_NUM_8
// #define CTRL_485    GPIO_NUM_19
// #define RX_485      GPIO_NUM_20

#define ROBOT_X1    GPIO_NUM_3
#define ROBOT_X2    GPIO_NUM_46
#define ROBOT_X3    GPIO_NUM_9
#define ROBOT_X4    GPIO_NUM_10
#define ROBOT_X5    GPIO_NUM_11
#define ROBOT_X6    GPIO_NUM_12


#define ROBOT_Y1    GPIO_NUM_45
#define ROBOT_Y2    GPIO_NUM_48
#define ROBOT_Y3    GPIO_NUM_47
#define ROBOT_Y4    GPIO_NUM_21
#define ROBOT_Y5    GPIO_NUM_14
#define ROBOT_Y6    GPIO_NUM_13

#define ROBOT_LED1    GPIO_NUM_35
#define ROBOT_LED2    GPIO_NUM_18

#define CAN_TX_GPIO    GPIO_NUM_1
#define CAN_RX_GPIO    GPIO_NUM_2


// #define TAG "RS485_ECHO_APP"
#define ECHO_TEST_TXD   (8)
#define ECHO_TEST_RXD   (20)

// RTS for RS485 Half-Duplex Mode manages DE/~RE
#define ECHO_TEST_RTS   (17)

// CTS is not used in RS485 Half-Duplex Mode
#define ECHO_TEST_CTS   (UART_PIN_NO_CHANGE)
#define BUF_SIZE        (127)

#define ECHO_UART_PORT          (UART_NUM_2)
#define PACKET_READ_TICS        (100 / portTICK_RATE_MS)
#define ECHO_READ_TOUT          (3) // 3.5T * 8 = 28 ticks, TOUT=3 -> ~24..33 ticks

#define BYTE0(dwTemp)           (*(char *)(&dwTemp))
#define BYTE1(dwTemp)           (*(char *)(&dwTemp)+1)
#define BYTE2(dwTemp)           (*(char *)(&dwTemp)+2)
#define BYTE3(dwTemp)           (*(char *)(&dwTemp)+3)

esp_vfs_spiffs_conf_t file_conf = {
    .base_path = "/spiffs",
    .partition_label = NULL,
    .max_files = 5,
    .format_if_mount_failed = true
};

esp_vfs_littlefs_conf_t littlefs_conf = {
    .base_path = "/littlefs",
    .partition_label = "littlefs",
    .format_if_mount_failed = true,
    .dont_mount = false,
};

typedef struct {
    int timer_group;
    int timer_idx;
    int alarm_interval;
    bool auto_reload;
} example_timer_info_t;

typedef struct {
    example_timer_info_t info;
    uint64_t timer_counter_value;
} example_timer_event_t;


static const twai_timing_config_t t_config = TWAI_TIMING_CONFIG_500KBITS();
static const twai_filter_config_t f_config = TWAI_FILTER_CONFIG_ACCEPT_ALL();
static const twai_general_config_t g_config = TWAI_GENERAL_CONFIG_DEFAULT(CAN_TX_GPIO, CAN_RX_GPIO, TWAI_MODE_NO_ACK);

esp_err_t event_handler(void *ctx, system_event_t *event)
{
    return ESP_OK;
}


unsigned long mysqrt(unsigned long x)
{
 register unsigned long xr;  // result register
 register unsigned long q2;  // scan-bit register
 register unsigned char f;   // flag (one bit)

 xr = 0;                     // clear result
 q2 = 0x40000000L;           // higest possible result bit
 do
 {
   if((xr + q2) <= x)
   {
     x -= xr + q2;
     f = 1;                  // set flag
   }
   else{
     f = 0;                  // clear flag
   }
   xr >>= 1;
   if(f){
     xr += q2;               // test flag
   }
 } while(q2 >>= 2);          // shift twice
 if(xr < x){
   return xr +1;             // add for rounding
 }
 else{
   return xr;
 }
}

//电机1参数
long tar_pulse1=0;
long cur_pulse1=0;
long pre_pulse1=0;
long pulse1_scale=0;
int8_t step1_up_foc = 100;
int8_t step1_down_foc = 100;

//电机2参数
long tar_pulse2=0;
long cur_pulse2=0;
long pre_pulse2=0;
long pulse2_scale=0;
int8_t step2_up_foc = 100;
int8_t step2_down_foc = 100;

//电机3参数
long tar_pulse3=0;
long cur_pulse3=0;
long pre_pulse3=0;
long pulse3_scale=0;
int8_t step3_up_foc = 100;
int8_t step3_down_foc = 100;

//电机4参数
long tar_pulse4=0;
long cur_pulse4=0;
long pre_pulse4=0;
long pulse4_scale=0;
int8_t step4_up_foc = 100;
int8_t step4_down_foc = 100;

//电机5参数
long tar_pulse5=0;
long cur_pulse5=0;
long pre_pulse5=0;
long pulse5_scale=0;
int8_t step5_up_foc = 100;
int8_t step5_down_foc = 100;

//电机6参数
long tar_pulse6=0;
long cur_pulse6=0;
long pre_pulse6=0;
long pulse6_scale=0;
int8_t step6_up_foc = 100;
int8_t step6_down_foc = 100;

//机械臂参数
long robot_tar_pulse = 0;
long robot_cur_pulse = 0;
long robot_global_speed = 50;
long robot_tar_speed = 100;
long robot_cur_speed = 0;
long robot_tar_acc = 100;
long robot_cur_acc = 0;
unsigned long robot_key= 0; //1-12 bit : control , 13- bit : continue or pause  , 17-32bit : IO 
long robot_model= 0;//  0:lock , 1:control , 2:joint move , 3:line move ,  3:arc move 
long comtrol_time_out = 500; //500ms
int time_is_run = 0;
int is_send_twai = 0;
int robot_foc[6];
// char file_string[20000];

int is_step4_run = 0;

long system_val[200];

static wl_handle_t s_wl_handle = WL_INVALID_HANDLE;

static QueueHandle_t tx_task_queue;
typedef enum {
    TX_SEND_PINGS,
    TX_SEND_START_CMD,
    TX_SEND_STOP_CMD,
    TX_TASK_EXIT,
    TX_SEND_DATA1,
    TX_SEND_DATA2,
    TX_SEND_DATA3,
} tx_task_action_t;

long max(long a, long b){
	if(a>b)return a;
	else return b;
}


void robot_change_pulse(){
	robot_tar_pulse = max(labs(tar_pulse1-cur_pulse1),labs(tar_pulse2-cur_pulse2));
	robot_tar_pulse = max(robot_tar_pulse,labs(tar_pulse3-cur_pulse3));
	robot_tar_pulse = max(robot_tar_pulse,labs(tar_pulse4-cur_pulse4));
	robot_tar_pulse = max(robot_tar_pulse,labs(tar_pulse5-cur_pulse5));
	robot_tar_pulse = max(robot_tar_pulse,labs(tar_pulse6-cur_pulse6));
	if(robot_tar_pulse!=0)
	{
		pulse1_scale=1000*labs(tar_pulse1-cur_pulse1)/robot_tar_pulse;
		pulse2_scale=1000*labs(tar_pulse2-cur_pulse2)/robot_tar_pulse;
		pulse3_scale=1000*labs(tar_pulse3-cur_pulse3)/robot_tar_pulse;
		pulse4_scale=1000*labs(tar_pulse4-cur_pulse4)/robot_tar_pulse;
		pulse5_scale=1000*labs(tar_pulse5-cur_pulse5)/robot_tar_pulse;
		pulse6_scale=1000*labs(tar_pulse6-cur_pulse6)/robot_tar_pulse;
	}
	robot_tar_pulse  = robot_tar_pulse*1000;
	robot_cur_pulse = 0;

}


int level2 = 0;
long num=0;
long L1=10,L2=30,L3=20;



int num1=0;
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

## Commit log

2021-10-21 新建 3D模型图
2021-10-21 新建 程序文件
2021-10-21 重命名 3D模型图/力传感器4.FCStd 为 3D模型图/力传感器.FCStd
    [力传感器.FCStd]
2021-10-21 更新程序
2022-05-27 新建 MC3
2022-05-27 重命名 MC3 为 MC3监控系统
2022-07-16 新建 图片
2022-08-18 add 图片/1.txt.
2022-08-18 add 图片/1.md.
2022-08-18 update 图片/1.md.
2022-08-18 update 图片/1.txt.
2022-09-19 删除文件 MC3监控系统
2022-09-19 删除文件 程序文件
2022-09-19 add 控制器程序.
2022-09-19 删除文件 控制器程序
2022-09-19 新建 控制器程序
2022-09-19 删除文件 图片/1.md
2022-09-19 删除文件 图片/1.txt
2022-09-19 删除文件 图片.png
2022-09-19 删除文件 机械臂开发购买零件.docx
2022-09-19 删除文件 力传感器电路图
    [力传感器-B_Cu.gbr, 力传感器-B_Mask.gbr, 力传感器-B_Paste.gbr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]
2022-09-19 新建 由于文件太大无法上传请带立创开源下载
2022-09-19 删除文件 3D模型图/6轴机械臂.FCStd
2022-09-19 删除文件 3D模型图/力传感器.FCStd
    [力传感器.FCStd]
2022-09-19 删除文件 3D模型图/机械臂blender仿真.blend
2022-09-19 add 3D模型图/由于文件太大无法上传请带立创开源下载.
2022-09-19 删除文件 3D模型图/由于文件太大无法上传请带立创开源下载
2022-09-19 update 3D模型图/由于文件太大无法上传请带立创开源下载.
2023-01-06 重命名 控制器程序 为 程序
2023-01-06 删除文件 程序/robot.zip
2023-01-06 删除文件 程序/firmware37.bin
2023-01-06 删除文件 程序/robot.c
2023-01-06 删除文件 程序/step1-1.c
2023-01-06 重命名 3D模型图 为 3D模型
